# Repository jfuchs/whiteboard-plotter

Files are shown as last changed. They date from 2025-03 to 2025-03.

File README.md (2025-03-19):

# whiteboard-plotter

A whiteboard plotter.

This is a functional whiteboard plotter, but the documentation here is a work in
progress. If you think you'd like to build one of these, and better instructions
would be helpful, please open an issue!

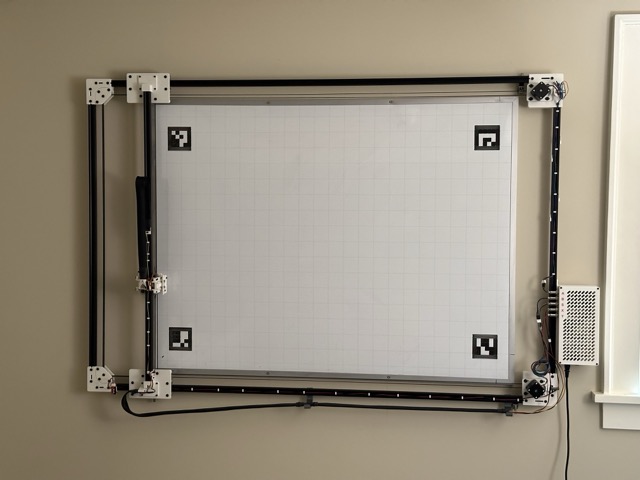
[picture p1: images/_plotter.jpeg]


## Features

- 1139mm x 798mm print area
- 2x NEMA 17 motors
- Core XY
- Largely made from PLA printed parts and 20x20mm v-slot aluminum extrusion

## Non-printed parts

A partial list of parts that need to be purchased. This is a work in progress.

| Part | Quantity | Purchase options | Notes |
| --- | --- | --- | --- |
| FluidNCTMC2209 Pen Laser V2 | 1 | [Tindie](https://www.tindie.com/products/33366583/tmc2209-penlaser-cnc-controller/), [Elecrow](https://www.elecrow.com/tmc2209-pen-laser-fluidnc-cnc-controller.html) |
| Mean Well LRS-50-24 power supply | 1 | [Amazon](https://www.amazon.com/LRS-50-24-Switching-Supply-Single-Output/dp/B019GYODAS) |
| C14 power inlet, switched | 1 | [Amazon](https://www.amazon.com/FILSHU-Rocker-Switch-Socket-Module/dp/B09LGX9MQX) |
| 20x20mm v-slot aluminum extrusion, 1000mm | 3 | |
| 20x20mm v-slot aluminum extrusion, 1500mm | 2 | |
| NEMA 17 stepper motor | 2 | |
| 9g servo | 1 | |
| 1/8" brass rod, ??mm | 2 |
| Spring from a clicky pen | 1 | | find one that can fit around the brass rod |
| V-slot wheels | 12 |
| 6mm GT2 Belt, ~6m | 2 |
| Idler pulley, toothless | ? |
| Idler pulley, toothed | ? |
| Drive pulley | 2 | | should fit on your stepper motor shaft |
| M3 hardware | lots | | various lengths, mostly socket cap |
| M5 hardware | lots | | various lengths, mostly button cap |
| Tape measure, preferrably used | 1 | | used for the drag chains |
| Mesh wire loom | ~3m | | wraps tape measure drag chains |
| Whiteboard | 1 | | ~3' x ~4' |
| Markers | ? | | Quartet bullet tip dry erase markers are great |
| Wire | lots | | |
| Connectors | ? | | dupont? jst-xh? airplane? |

## Printed parts

| Part | Quantity | Notes |
| --- | --- | --- |
| a_motor_corner_bracket.stl | 1 | support needed inside the channels that receieve aluminum rails |
| actuator_plate.stl | 1 |
| b_motor_corner_bracket.stl | 1 | support needed inside the channels that receieve aluminum rails |
| bottom_gantry_carriage.stl | 1 |
| bottom_gantry_carriage_cover.stl | 1 | probably bridgeable without support |
| enclosure_body.stl | 1 |
| enclosure_bracket.stl | 1 |
| enclosure_top.stl | 1 |
| gantry_rail_drag_chain_block.stl | 1 |
| helical_gear.stl | 1 |
| helical_rack.stl | 1 |
| hot_shoe_mount.stl | 1 |
| idler_corner_bracket.stl | 2 |
| idler_plate_back.stl | 2 |
| idler_plate_front.stl | 2 |
| marker_clamp.stl | 1 | print more if you have more markers |
| motor_plate.stl | 2 |
| rod_end_block.stl | 2 |
| servo_bracket.stl | 1 |
| shuttle.stl | 1 |
| top_gantry_carriage.stl | 1 |
| top_gantry_carriage_cover.stl | 1 | probably bridgeable without support |
| y_carriage.stl | 1 |
| y_carriage_brace_bottom.stl | 1 |
| y_carriage_brace_top.stl | 1 |
| y_carriage_drag_chain_block.stl  | 1 |
| y_undercarriage.stl | 1 |

## Assembly

This is a rough outline of the steps.

1. Fixed parts
   1. Print the parts
   2. Assemble the frame
   3. Mount the whiteboard and frame to the wall, such that the frame is ??mm
      from the whiteboard
2. Carriages and gantry
   1. Attach the gantry carriages to the horizontal frame rails
   2. Attach the gantry rail to the gantry carriages
   3. Attach the y carriage to the gantry rail
3. Belts and motors
   1. Attach the motors to the motor plates
   2. Route the belt
   3. Attach the motor plates to the corner braces loosely
   4. Tension the belt by pulling the motor plates away from the center of the
      machine
   5. Tighten the motor plates to the corner braces
4. Enclosure
   1. Wire from the power inlet to the power supply
   2. Wire from the power supply to the controller
   3. Wire from the controller to the five ports
5. Wiring
   1. Attach the drag chains
   2. Wire from motors to enclosure
   3. Wire from servo to enclosure
   4. Attach end stops
   5. Wire from end stops to enclosure
6. Configure
   1. Install the fluidnc yaml config file.

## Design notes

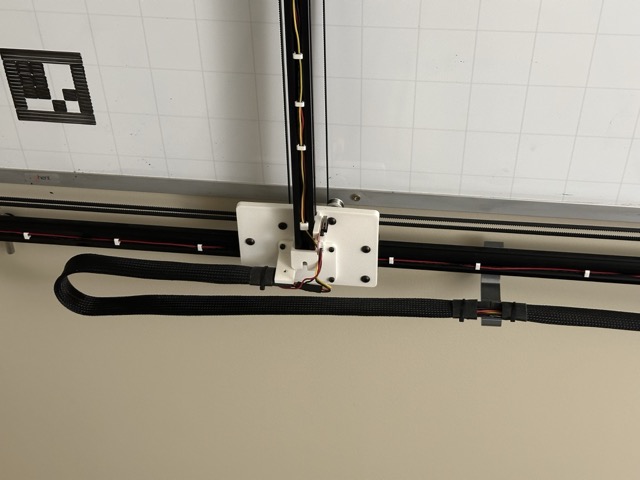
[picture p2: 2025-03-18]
images/drag_chain_x.jpeg

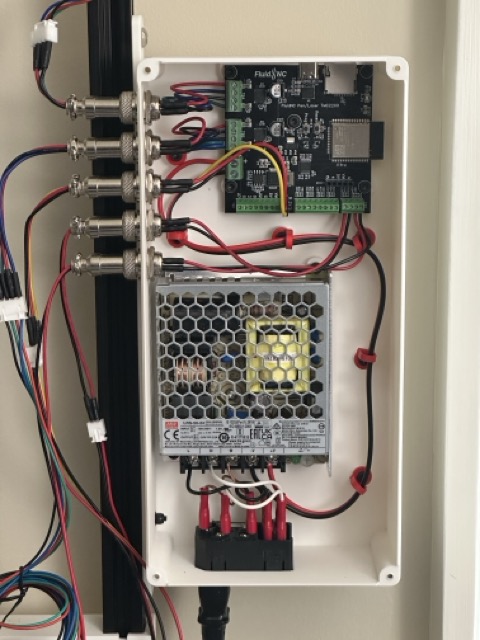
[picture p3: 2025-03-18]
images/enclosure_open.jpeg

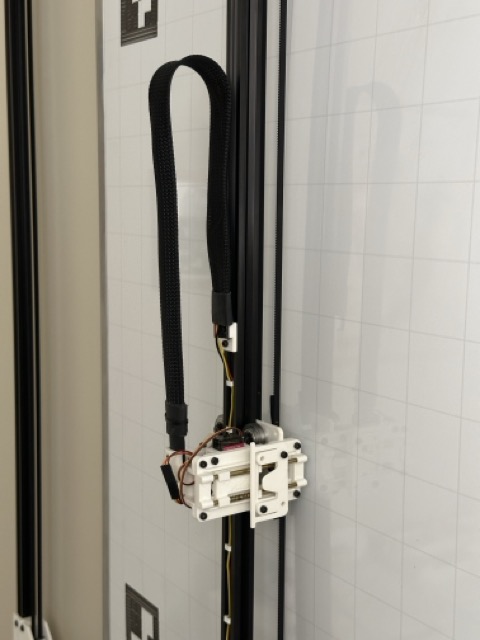
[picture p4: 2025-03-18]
images/drag_chain_y.jpeg

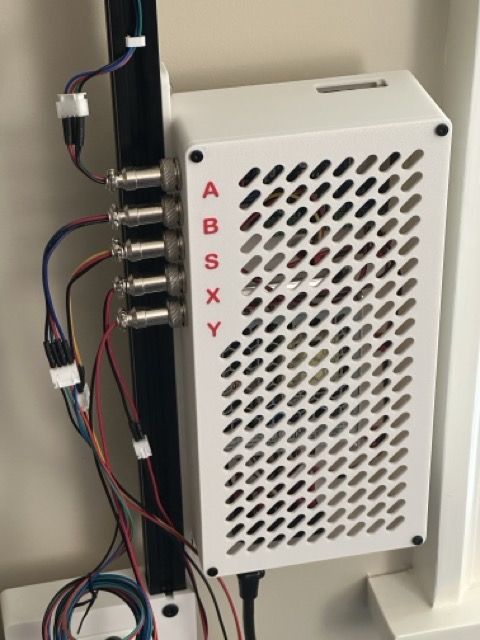
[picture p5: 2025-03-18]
images/enclosure_closed.jpeg

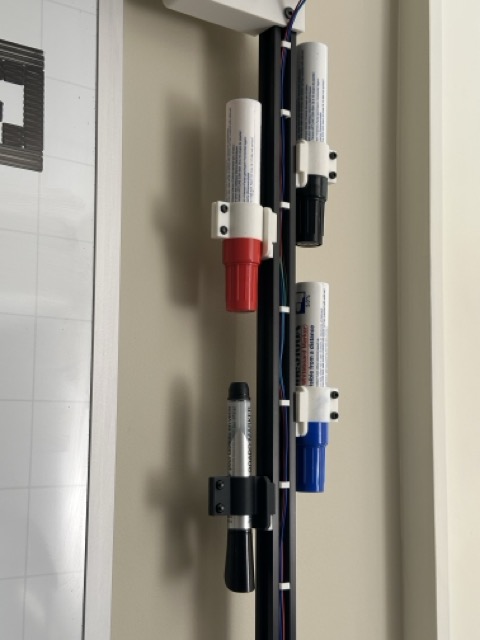
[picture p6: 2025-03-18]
images/markers.jpeg

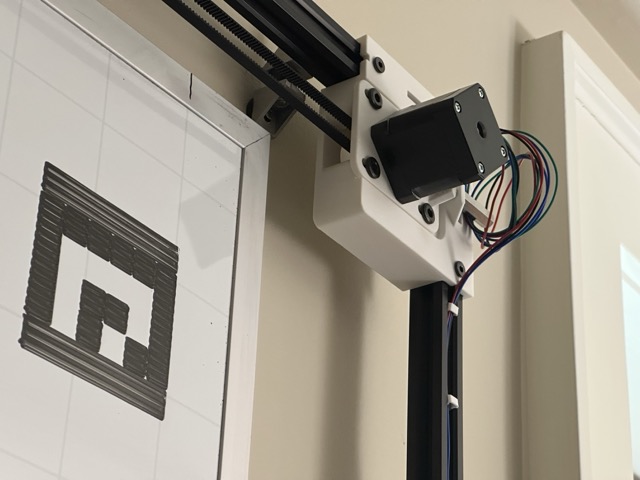
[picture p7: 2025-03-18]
images/motor_a.jpeg

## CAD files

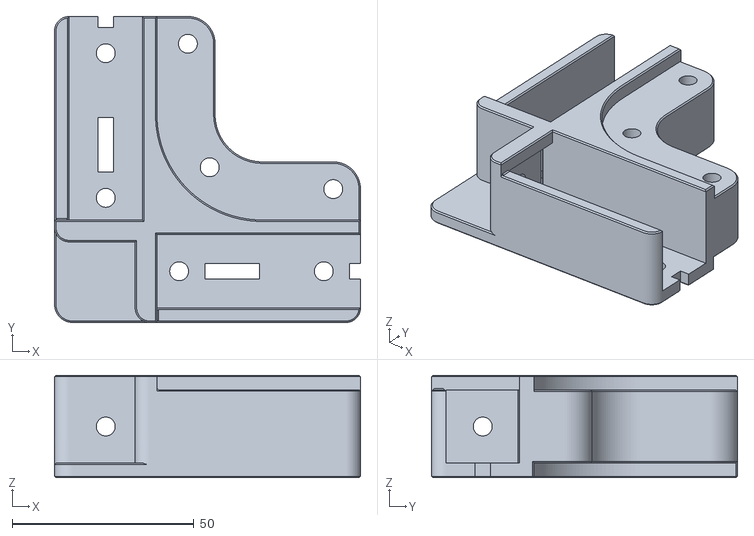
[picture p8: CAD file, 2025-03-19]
printed_parts/idler_corner_bracket.stl
84.2 x 84.2 x 28.2

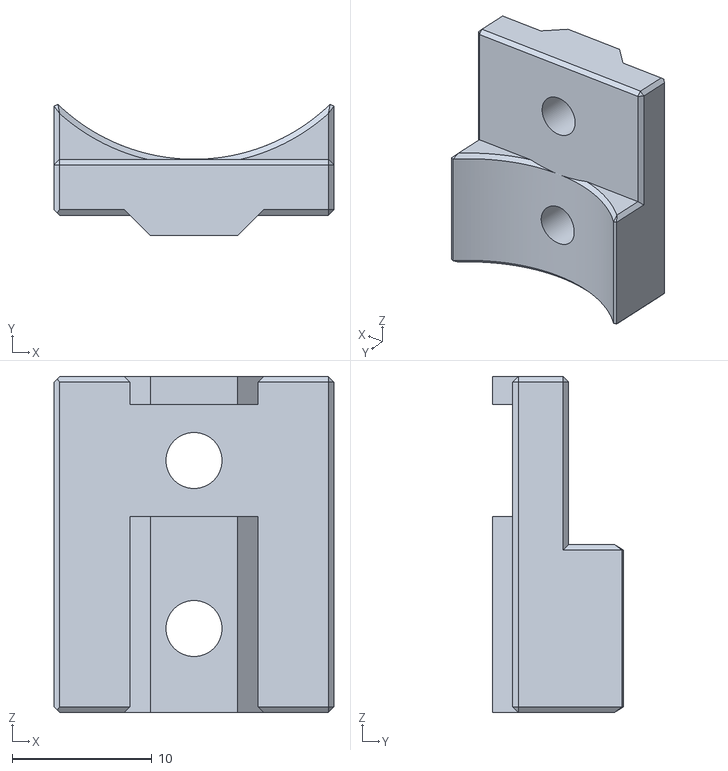
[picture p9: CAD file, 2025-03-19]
printed_parts/gantry_rail_drag_chain_block.stl
20.0 x 9.37 x 24.0

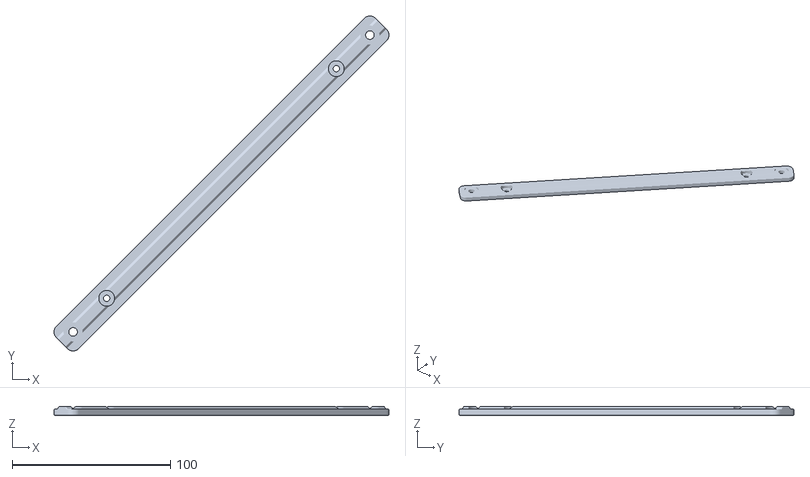
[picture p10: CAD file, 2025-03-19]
printed_parts/enclosure_bracket.stl
211.5 x 211.5 x 5.45

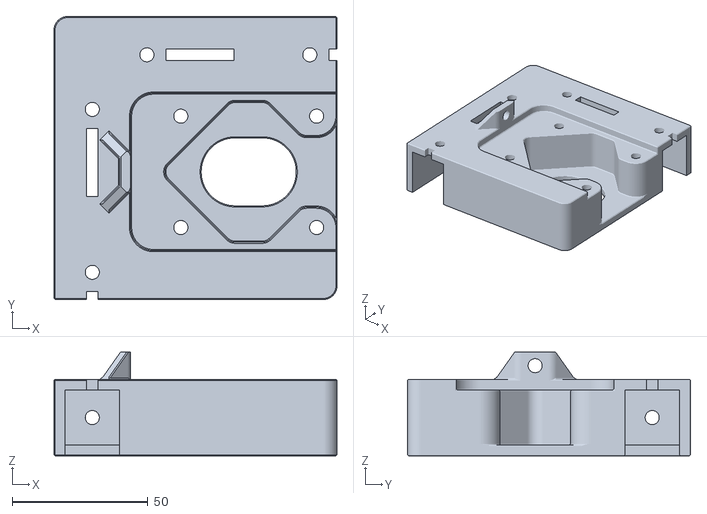
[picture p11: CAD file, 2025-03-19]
printed_parts/b_motor_corner_bracket.stl
104.2 x 104.2 x 38.2

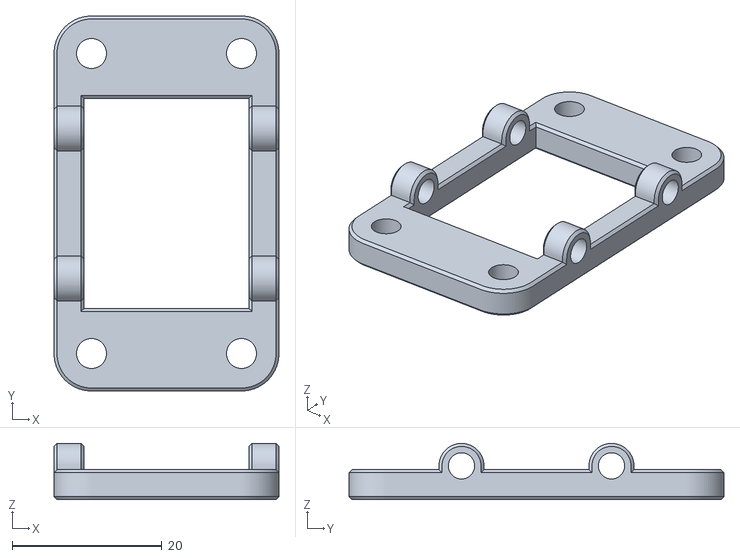
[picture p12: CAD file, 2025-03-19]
printed_parts/shuttle.stl
30.0 x 50.0 x 7.50

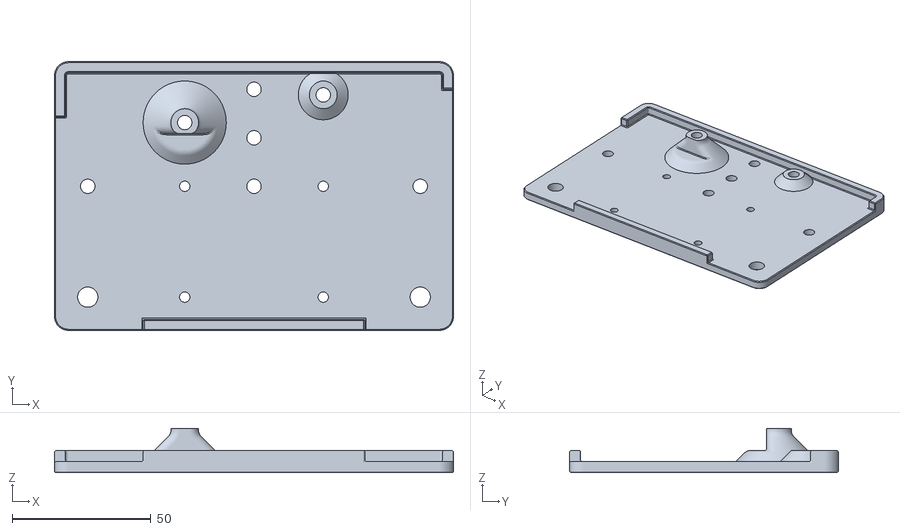
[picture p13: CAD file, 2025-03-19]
printed_parts/top_gantry_carriage.stl
144.0 x 97.0 x 16.0

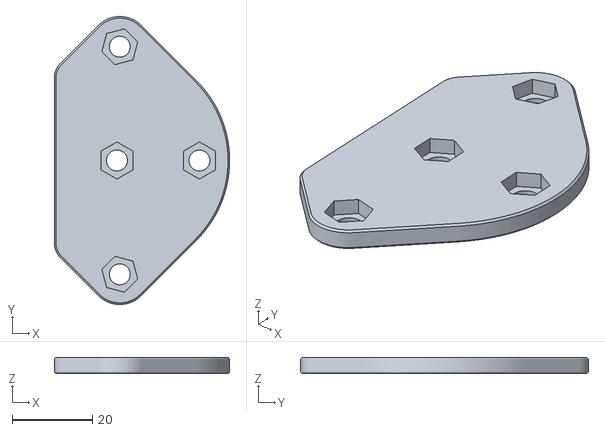
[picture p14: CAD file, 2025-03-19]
printed_parts/idler_plate_back.stl
43.6 x 71.6 x 4.00

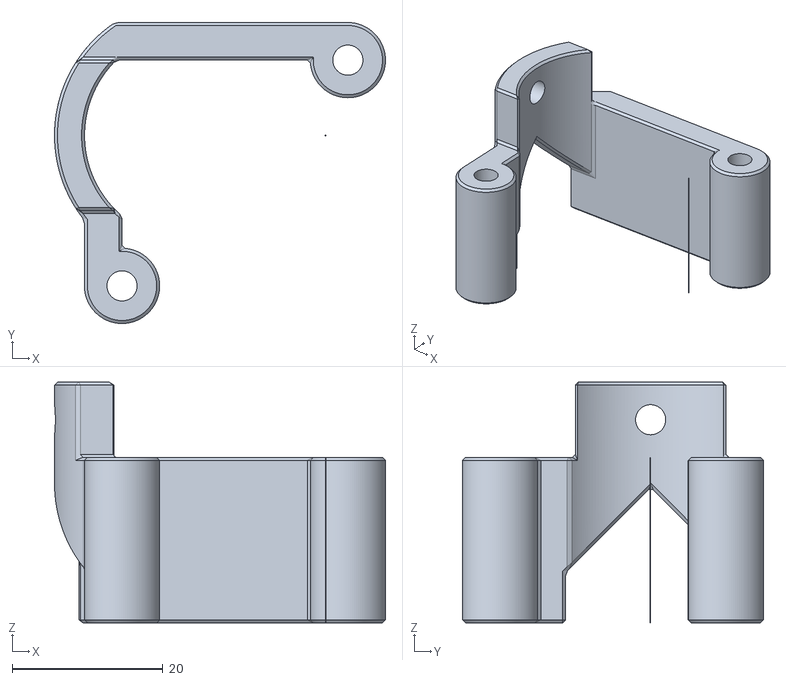
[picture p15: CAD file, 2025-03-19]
printed_parts/y_carriage_drag_chain_block.stl
44.0 x 40.0 x 32.0

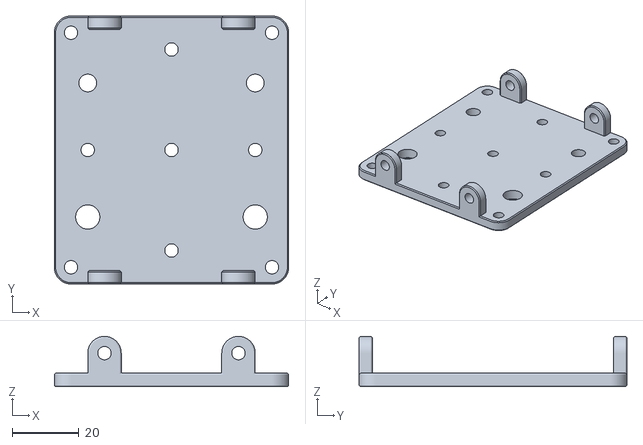
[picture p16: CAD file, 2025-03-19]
printed_parts/y_carriage.stl
70.0 x 80.0 x 15.0

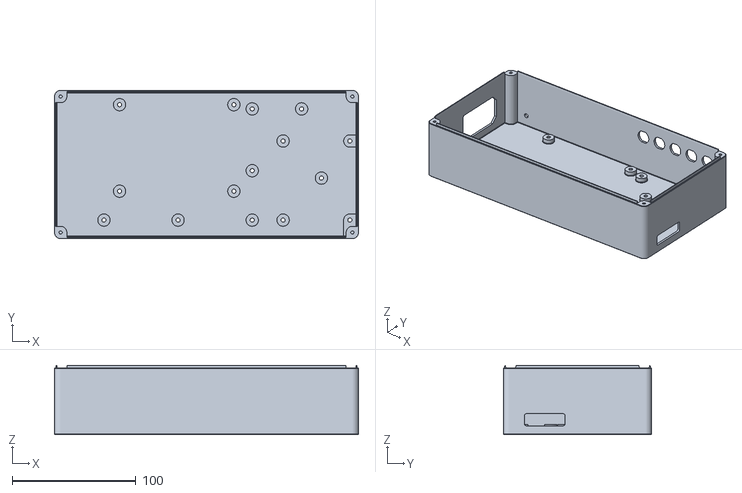
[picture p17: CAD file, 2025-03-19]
printed_parts/enclosure_body.stl
246.0 x 120.0 x 56.0

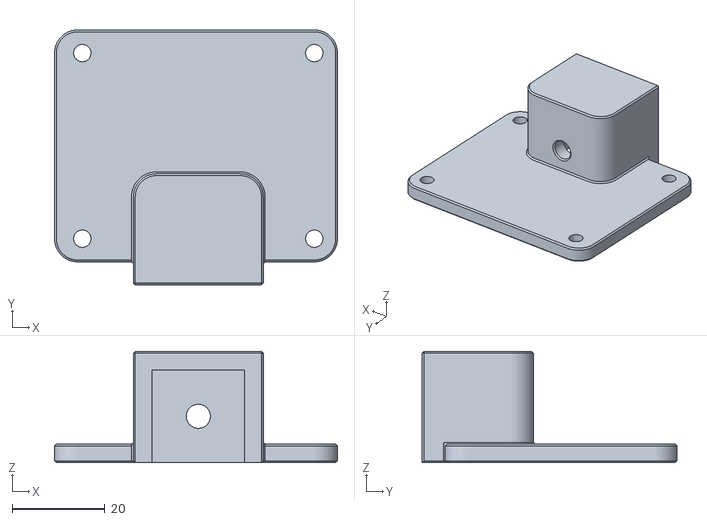
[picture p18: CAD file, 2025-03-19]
printed_parts/top_gantry_carriage_cover.stl
61.0 x 55.0 x 24.0

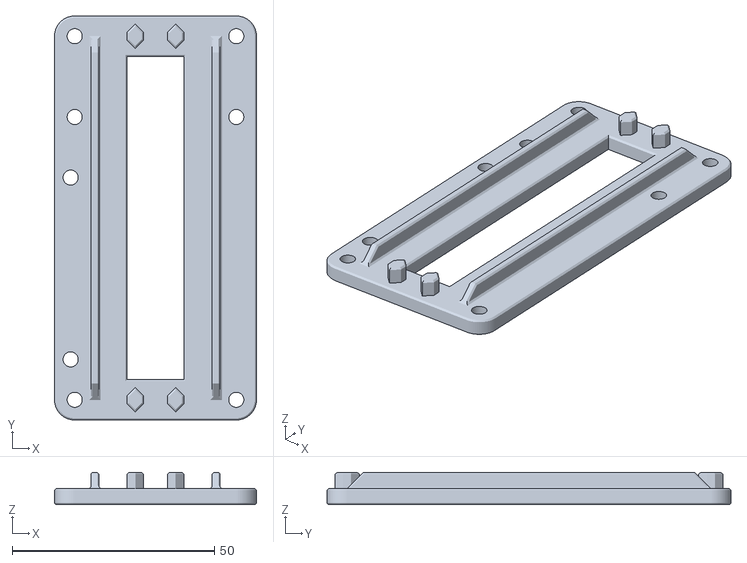
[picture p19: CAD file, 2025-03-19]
printed_parts/actuator_plate.stl
50.0 x 100.0 x 8.00

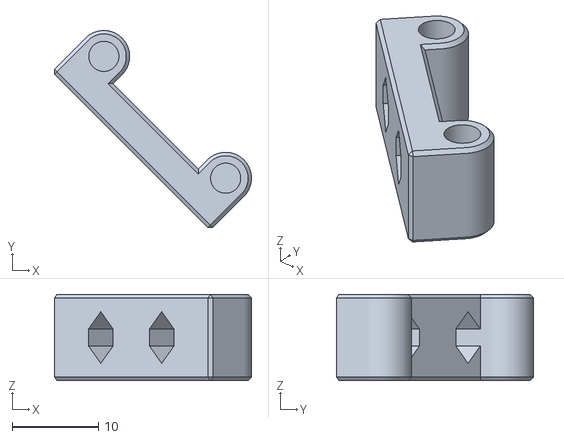
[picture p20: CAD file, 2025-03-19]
printed_parts/rod_end_block.stl
22.9 x 22.9 x 10.0

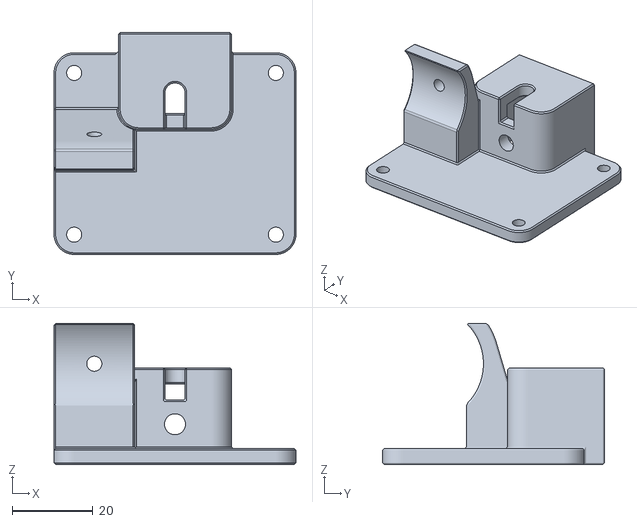
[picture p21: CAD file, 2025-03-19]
printed_parts/bottom_gantry_carriage_cover.stl
60.0 x 55.0 x 35.0

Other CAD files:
printed_parts/a_motor_corner_bracket.stl
printed_parts/helical_gear.stl
printed_parts/idler_plate_front.stl
printed_parts/motor_plate.stl
printed_parts/bottom_gantry_carriage.stl
printed_parts/enclosure_top.stl
printed_parts/helical_rack.stl
printed_parts/hot_shoe_mount.stl
printed_parts/idler_corner_bracket(1).stl
printed_parts/idler_plate_back(1).stl
printed_parts/idler_plate_front(1).stl
printed_parts/marker_clamp.stl
printed_parts/motor_plate(1).stl
printed_parts/rod_end_block(1).stl
printed_parts/servo_bracket.stl
printed_parts/y_carriage_brace_bottom.stl
printed_parts/y_carriage_brace_top.stl
printed_parts/y_undercarriage.stl

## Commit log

2025-03-19 Add STLs for parts
    [a_motor_corner_bracket.stl, actuator_plate.stl, b_motor_corner_bracket.stl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]
2025-03-19 Assembly instruction improvement
